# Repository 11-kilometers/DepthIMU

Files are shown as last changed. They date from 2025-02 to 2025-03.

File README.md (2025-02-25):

The most important information needed for underwater navigation is how deep you are and what direction you're pointing. ROVs, AUVs, and even more passive marine systems need this information, so we've created a Depth/ IMU module for this purpose. The design is focused on robustness. It uses a Keller 7LD depth sensor which can be submerged for long periods of time, and a BNO 085 Inertial Measurment Unit (IMU) that has a 3-axis magnatometer, a 3-axis gyrometer, and a 3-axis magnitometer. The system uses the Bristlemouth underwater connectivity standard to communicate and get power, and the PCB has been designed to mate with a Bristlemouth Mote made by Sofar Ocean Technologies. The board is designed in KiCAD 8.0.4.

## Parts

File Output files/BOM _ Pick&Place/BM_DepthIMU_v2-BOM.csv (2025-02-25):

Comment | Designator | Footprint | JLCPCB Part #
100nF 16V X5R | C1,C2,C3 | Capacitor_SMD:C_0201_0603Metric | C5677646
DF17(2.0)-30DP-0.5V(57) | J1 | Hirose Connectors:DF172030DP05V57
10K 25V 50mW | R1 | Resistor_SMD:R_0201_0603Metric | C253350
2K2 25V 50mW | R2,R3 | Resistor_SMD:R_0201_0603Metric | C239976
0R 25V 50mW | R5 | Resistor_SMD:R_0201_0603Metric | C170193
BNO085 | U1 | Sensor Motion BNO085:IC_BNO085 | C5189642

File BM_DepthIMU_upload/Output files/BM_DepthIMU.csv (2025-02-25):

Id | Designator | Footprint | Quantity | Designation | Supplier and ref
1 | C3,C2,C1 | C_0201_0603Metric | 3 | 100nF
2 | FD3,FD1,FD2,FD5,FD6,FD4 | Fiducial_0.5mm_Mask1mm | 6 | Fiducial_0.5mm_Mask1mm
3 | R4 | R_0201_0603Metric | 1 | DNP
4 | R3,R2 | R_0201_0603Metric | 2 | 2K2
5 | R1 | R_0201_0603Metric | 1 | 10K
6 | U1 | IC_BNO085 | 1 | BNO085
7 | J1 | DF172030DP05V57 | 1 | DF17_2.0_-30DP-0.5V_57_
8 | R5 | R_0201_0603Metric | 1 | 0R
9 | U2 | PA-7LD | 1 | Series 7LD

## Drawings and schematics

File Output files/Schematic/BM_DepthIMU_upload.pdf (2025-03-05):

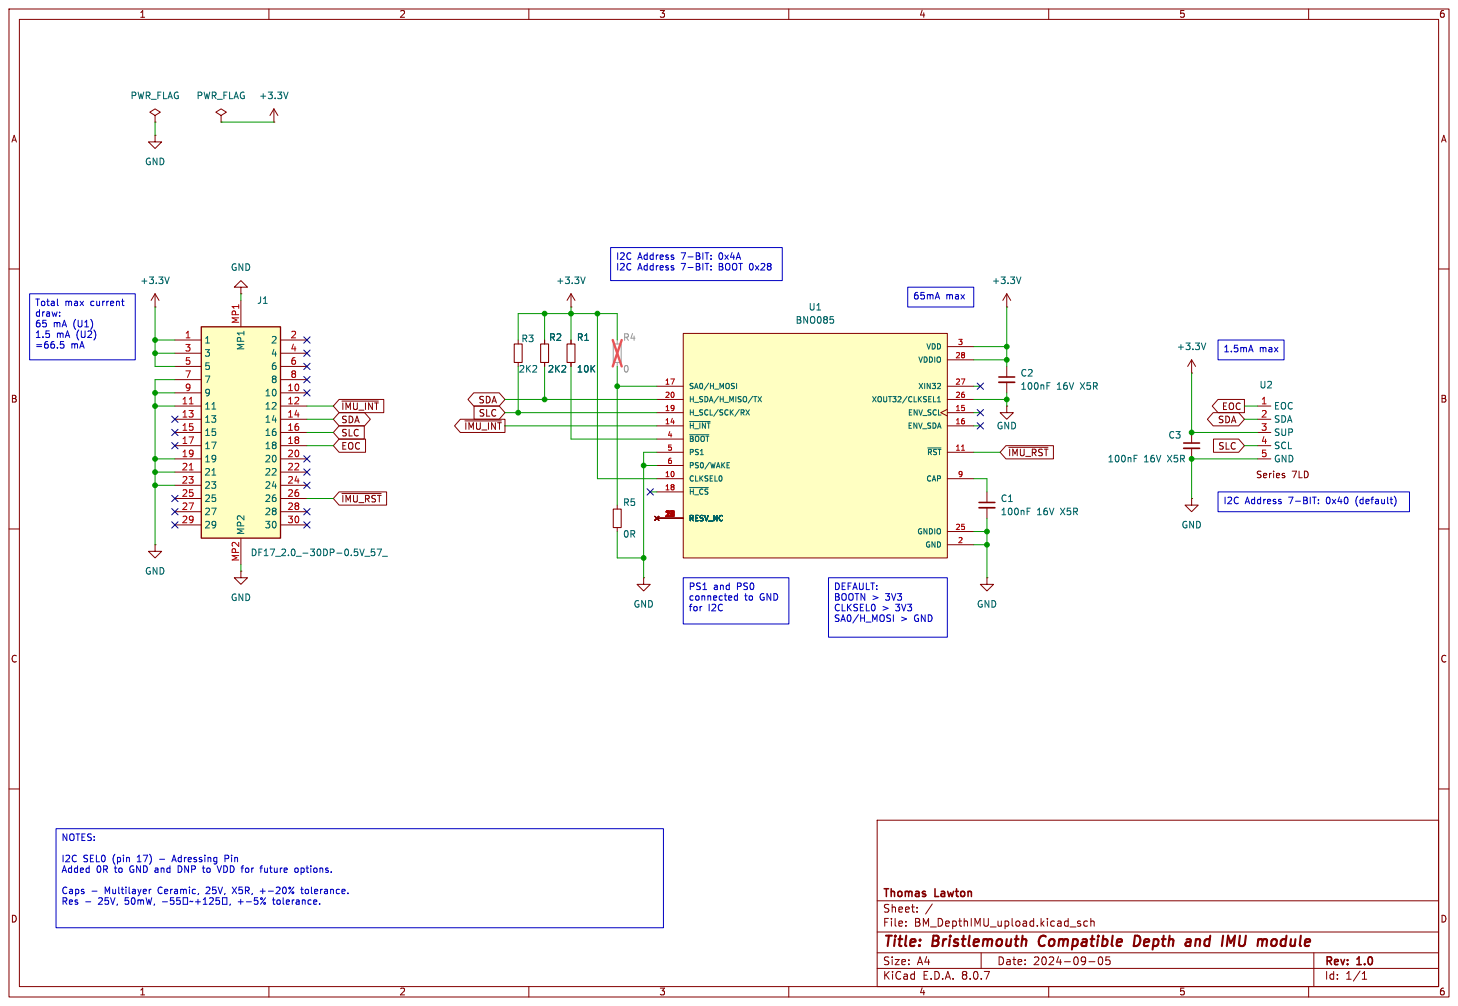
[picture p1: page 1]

EOC 1 SDA 2 SUP 3 SCL 4 GND 5U2 GND GND GND

I2C SEL0 (pin 17) - Adressing Pin Added 0R to GND and DNP to VDD for future options.

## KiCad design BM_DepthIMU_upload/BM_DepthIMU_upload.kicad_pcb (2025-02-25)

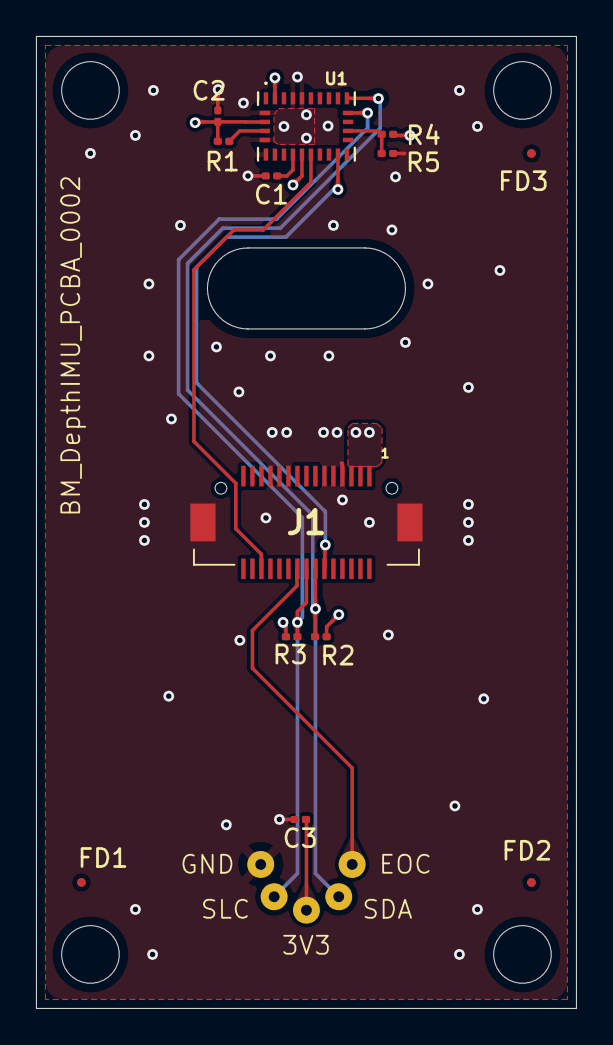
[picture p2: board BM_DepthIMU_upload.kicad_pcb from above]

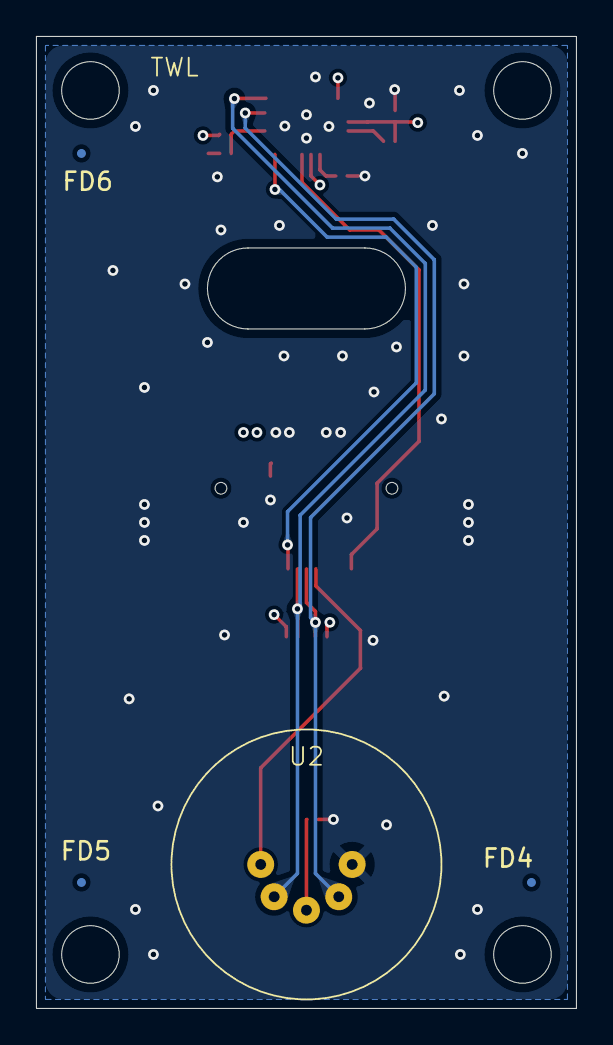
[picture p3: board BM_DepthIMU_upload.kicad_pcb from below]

Board: 4 copper layers, 30.0 x 54.0 mm, 17 parts (4 on the bottom side), 10 nets.

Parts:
C1, C2, C3: 100nF 16V X5R; C_0201_0603Metric
FD1, FD2, FD3, FD4, FD5, FD6: Fiducial_0.5mm_Mask1mm
J1: DF17_2.0_-30DP-0.5V_57_; DF172030DP05V57
R1: 10K; R_0201_0603Metric
R2, R3: 2K2; R_0201_0603Metric
R4: 0; R_0201_0603Metric
R5: 0R; R_0201_0603Metric
U1: BNO085; IC_BNO085
U2: Series 7LD; PA-7LD

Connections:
+3.3V: C2.1, C3.1, J1.1, J1.3, J1.5, R1.1, R2.1, R3.1, R4.1, U1.3 (VDD), U1.10 (CLKSEL0), U1.28 (VDDIO), U2.3 (SUP)
EOC: J1.18, U2.1 (EOC)
GND: C1.2, C2.2, C3.2, J1.7, J1.9, J1.11, J1.19, J1.21, J1.23, J1.MP1, J1.MP2, R5.2, U1.2 (GND), U1.5 (PS1), U1.6 (PS0/WAKE), U1.25 (GNDIO), U1.26 (XOUT32/CLKSEL1), U2.5 (GND)
unnamed: C1.1, U1.9 (CAP)
unnamed: R4.2, R5.1, U1.17 (SA0/H_MOSI)
unnamed: R1.2, U1.4 (~BOOT)
SDA: J1.14, R2.2, U1.20 (H_SDA/H_MISO/TX), U2.2 (SDA)
SLC: J1.16, R3.2, U1.19 (H_SCL/SCK/RX), U2.4 (SCL)
~IMU_INT: J1.12, U1.14 (~H_INT)
~IMU_RST: J1.26, U1.11 (~RST)

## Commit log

2025-02-25 Add files via upload
    KiCAD Schematic and Layout files for the DepthIMU PCB.
    [BM_DepthIMU.csv, BM_DepthIMU_upload.kicad_pcb, BM_DepthIMU_upload.kicad_sch]
2025-02-25 Add files via upload
    DepthIMU PCBA BOM, pick & place, gerber & drill files.
    [BM_DepthIMU_v2-BOM.csv, BM_DepthIMU_v2-BOM.xlsx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]
2025-03-05 Add files via upload
    PDF Schematic of the BM DepthIMU PCB
